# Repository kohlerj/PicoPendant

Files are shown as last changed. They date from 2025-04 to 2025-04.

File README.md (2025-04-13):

# PicoPendant

## Description

Inspired by the [CNC-Pendant-Firmware](https://github.com/Duet3D/CNC-Pendant-Firmware), I created a simple CNC pendant based on the cheap Raspberry Pico microcontroller to be used with Duet3D Ltd RepRapFirmware. 

It is compatible with all versions of the Pico microcontroller RP2040 and RP2350. Obviously also compatible with the boards, that is Pico 1, Pico 2, Pico W and Pico 2W.

This is the *only* the software side and some wiring instructions. We'll see if I can make a PCB for it in the future. For now you could try to reproduce [My BOM of the weekend ;)](https://github.com/kohlerj/PicoPendant?tab=readme-ov-file#one-night-project) which ended up in the pendant you see below.

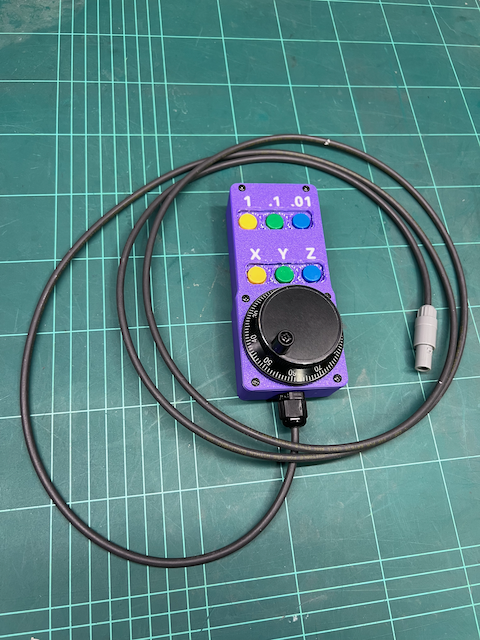
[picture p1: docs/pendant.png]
PicoPendant


## Features

- Axis selection XYZ
- Multiplier selection: 1X - 1mm, 10X - 0.1mm and 100X - 0.01mm
- Homing by holding Y for 2sec
- Reset by holding X and Z for 2sec

## An "open" BOM

A board (protoboard, PCB or some Frankenstein solution) with the following components:
- 1x Raspberry Pico (or compatible)
- 6x buttons with a normally open contact - e.g. https://www.aliexpress.com/item/32815260070.html
- 6x 5mm LEDs with adequate resistors - e.g. https://www.aliexpress.com/item/1005003144912658.html
- 1x Schottky diode (1N5819 or similar) - I'd say above 500mA to be safe, Vf as low as possible
- 2x logic level shifters to shift the encoder 5V A/B signals to 3.3V. I used LTV-817 optocouplers because it's what I had on hand. I guess a simple voltage divider would work if anything.

Aside from that you'll need:
- 1x 5V rotary encoder - e.g. https://www.aliexpress.com/item/1005008202737088.html
- A case, 3D printed most probably
- wires, cables, connectors and some screws

The Pico has a built-in Schmitt trigger action, enough for our purpose. No need to filter the inputs.

## Installation

1. Connect your pendant to a **3.3V compatible UART port** on your mainboard
    - You might need to define a new serial port in your `board.txt` file, e.g. by adding  `serial.aux2.rxTxPins={E.7, E.8}` to `board.txt`.
2. Add the following to your `config.g` file: 

```
M575 P1 S4 B57600 
```

  - P1 is the serial port number. Look at your board.txt for "aux" if you need another UART interface than the TFT or PanelDue dedicated one
  - S4 is required as we are using CRC to check for data integrity
  - B57600 is as configured in the precompiled version. You might need to adapt if you modify the code

3. That's it!

## One night project

I did not want to wait for a PCB so I went ahead a built a prototype on a protoboard together with a 3D printed case.

### BOM

 I used the following components:

- 1x protoboard 50x70mm, https://www.aliexpress.com/item/1005001854661430.html
- 1x Pico 2 board, https://www.digikey.ch/short/4wzqqnww
- 6x buttons, https://www.aliexpress.com/item/32815260070.html
- 6x LEDs with 100Ohm for the blue and 220Ohm resistors for the green LEDs, https://www.aliexpress.com/item/1005003144912658.html
- 1x Schottky diode (1N5819), https://www.digikey.ch/short/5j751j2j
- 2x LTV-817 DIP-4 optocouplers with 2x 1k resistors for the photodiode side, https://www.digikey.ch/short/rwcv58q7
- 1x 5V rotary encoder, https://www.aliexpress.com/item/1005008202737088.html
- 1x PG-7 gland, https://www.aliexpress.com/item/1005003296249352.html
- 1x 3-pin fake *ODU*-like connector, https://www.aliexpress.com/item/1005002002825883.html
- 4x 2x8mm self-tapping screws
- 6x 3x8mm self-tapping screws
- wires, cables, connectors

### Pins

The pre-compiled version uses the pinout found in the table below.

| Pin | Function | Comment |
|-----|---|---|
| GP0  | UART_TX | **3.3V** |
| GP4  | X axis LED | |
| GP5  | X axis button | internally pulled-up |
| GP10 | encoder A | **3.3V** |
| GP11 | encoder B | **3.3V** |
| GP12 | Y axis LED | |
| GP13 | Y axis button | internally pulled-up |
| GP14 | 1X LED | |
| GP15 | 1X button | internally pulled-up |
| GP16 | 10X LED | |
| GP17 | 10X button | internally pulled-up |
| GP18 | 100X LED | |
| GP19 | 100X button | internally pulled-up |
| GP20 | Z axis LED | |
| GP21 | Z axis button | internally pulled-up |
| VSYS | - | Connected to diode's **cathode** |

Refer to the [configuration section](https://github.com/kohlerj/PicoPendant/blob/main/PicoPendant.cpp#L44-L74) in `PicoPendant.cpp`.

### Wiring and schematics

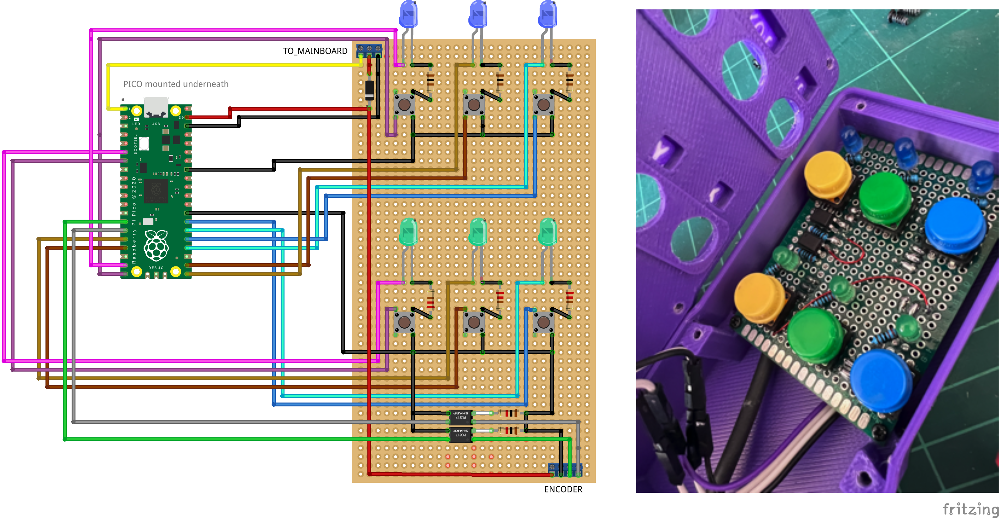
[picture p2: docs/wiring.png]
Wiring


Link to [schematics](./docs/schematics.png)

### Case

In the CAD folder, you'll find a STEP model of the case. The model includes built-in support and it is meant to be printed with a **layer height of .3mm**. It is a **multicolor** print. The letters need be printed in a translucent material while the case in an opaque one. 

If you do not have a multicolor printer, do the following:
1. Load the model with ALL subparts
2. Remove casing parts and built-in support. Keep only the letters
3. Export this job
4. Add the casing parts and built-in support back and remove the letters
5. Export this job
6. Combine the two jobs
    1. Open the first job and scroll until the end of print code is called. Remove the call and everything below
    2. Add a pause that will allow you to change the filament and come back at exactly the same spot
    3. Copy in the content of the second job
    4. Remove everything up to and including the print start code. 
    5. Tweak the code so that after the pause, the printer will move to the start position of the second job
    6. **Make sure nothing is overlapping**, the skirt in particular if you are using one!!!

The dimensions are **NOT** compensated for ABS, my material of choice. This means that it should print just fine on filament that shrinks less. For ABS, use your material shrinkage parameter or scale up the XY axes by 1%.

Support should come off easily with a flat screwdriver.

You might need to clear up the button holes a little bit. I made them already larger than my prototype but it is untested.

## License

This project is licensed under the MIT License - see the [LICENSE](LICENSE.txt) file for details.

In contains code from the Pico examples repository under BSD-3 license. See the [LICENSE](LICENSE.txt) file for details.

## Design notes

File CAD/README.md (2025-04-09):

# OnShape

The case was designed on OnShape: [Pendant](https://cad.onshape.com/documents/d751ca49352ebbe916205d74/w/4706b7efb3b0ea69cdef4548/e/34748dad4fb093fe07ba34ad)

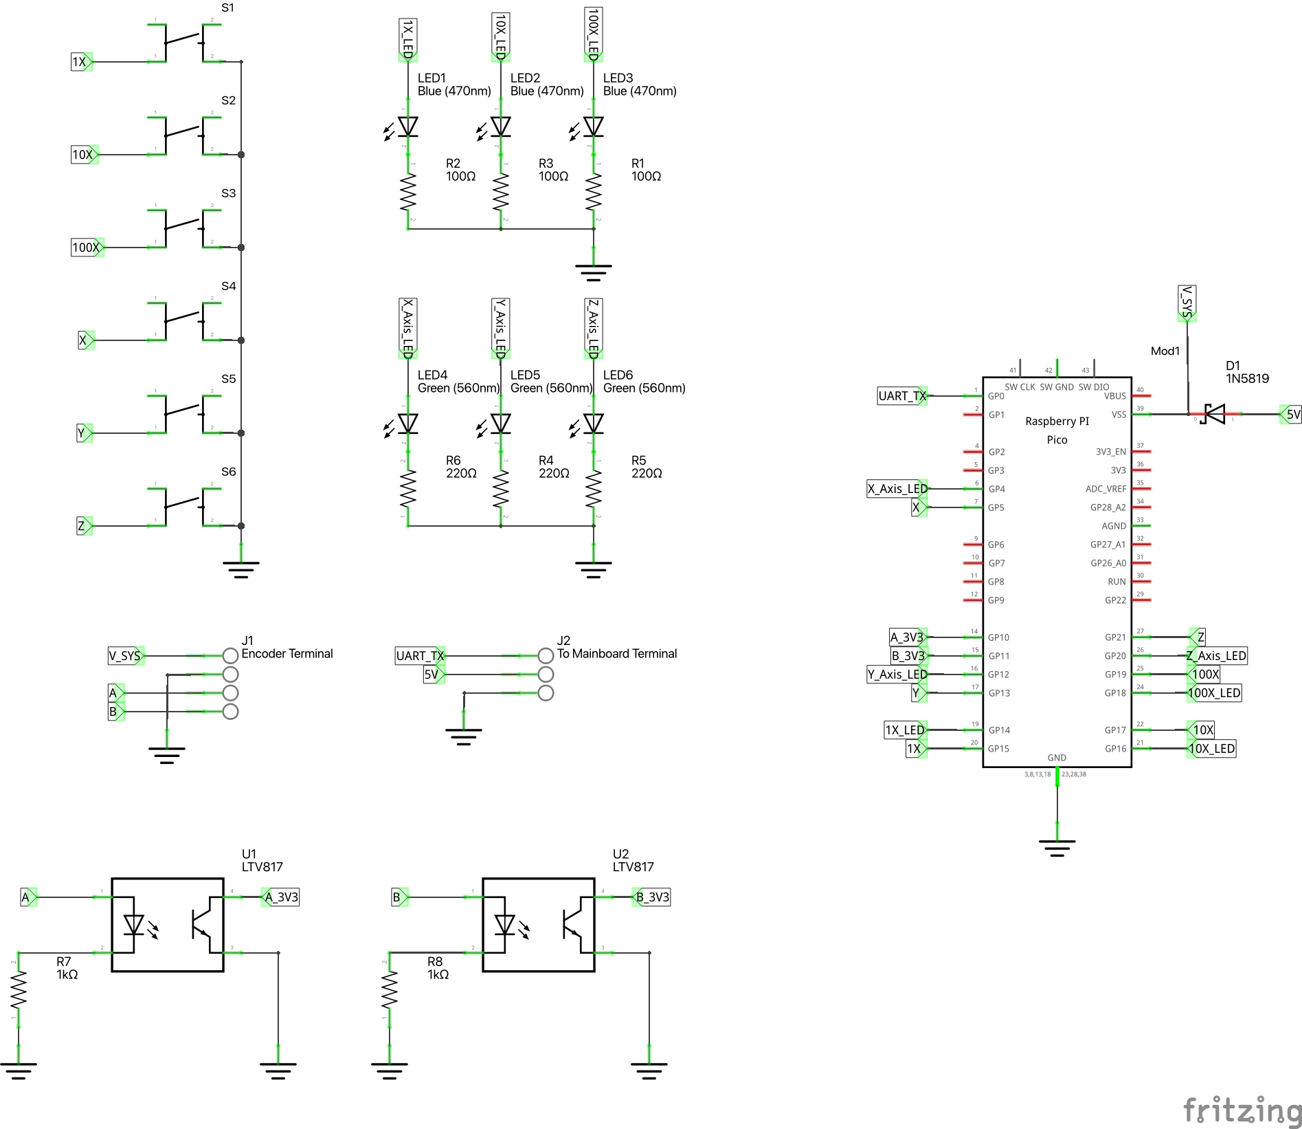
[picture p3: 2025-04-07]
docs/schematics.png

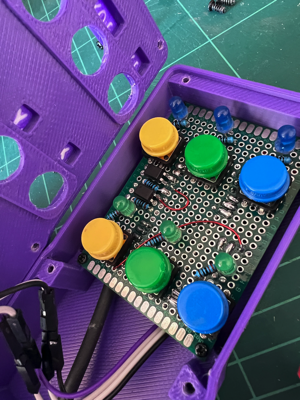
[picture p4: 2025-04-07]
docs/internals.png

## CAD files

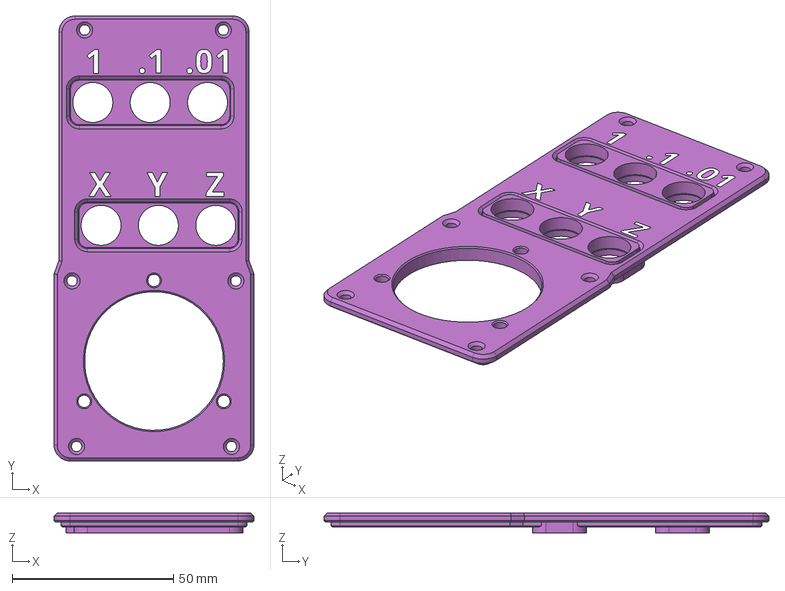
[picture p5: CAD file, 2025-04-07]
CAD/Cover.step
62.0 x 138.0 x 6.20 mm

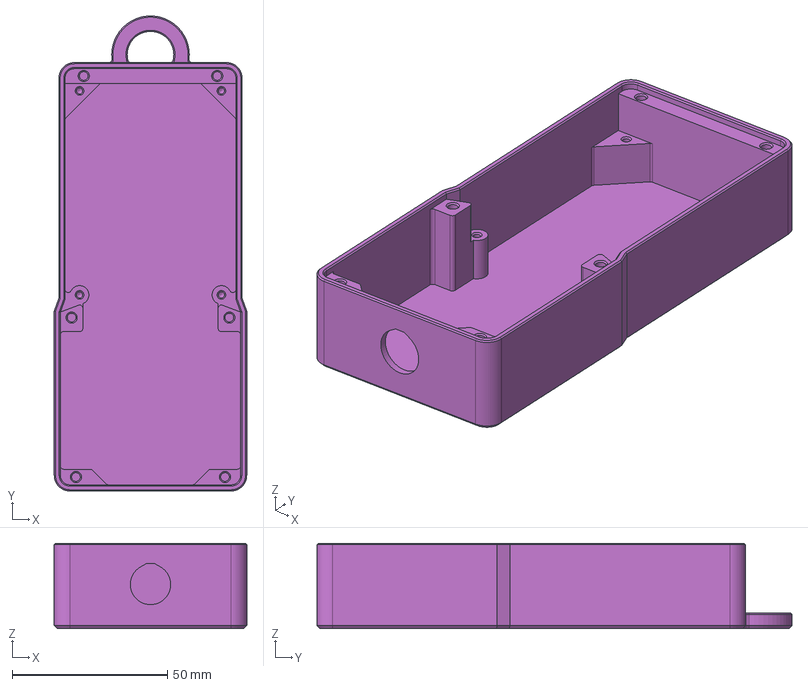
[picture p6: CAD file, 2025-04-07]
CAD/Base.step
62.0 x 153.0 x 27.5 mm

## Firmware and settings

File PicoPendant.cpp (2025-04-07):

/*******************************************************************************
 * File:        PicoPendant.cpp
 * Author:      Julien Kohler
 * Created:     2025-04-07
 *
 * Description: Based on CNC-Pendant from Duet and Raspberry Pi Pico Encoder
 *              example.
 * 
 *              Simply add M575 P1 S4 B57600 to your config.g file to enable the
 *              Duet3D pendant support.
 *              P is the serial port number
 *              S4 is the mode. This project uses CRC so mode 4 is required.
 *              B57600 is the baudrate that needs to match the value below
 *              
 *              User can select the axis and the multiplier using the buttons.
 *              The encoder is used to move the selected axis.
 *              The selected axis is indicated by the corresponding LED.
 *              The selected multiplier is indicated by the corresponding LED.
 * 
 *              The user can reset the printer by pressing the X and Z buttons for 
 *              2 seconds.
 * 
 *              The user can home the printer by pressing the Y button for 2 seconds.
 *           
 *
 * License:     This file is subject to the terms and conditions outlined in the
 *              LICENSE file located at the root of this project.
 *              (The LICENSE file may specify MIT, GPL, or another license.)
 ******************************************************************************/

#include <stdio.h>
#include "pico/stdlib.h"
#include "hardware/pio.h"
#include "hardware/timer.h"
#include "hardware/gpio.h"

#include "quadrature_encoder.pio.h"
#include <string>
#include <string_view>
#include <format>

#define UART uart0

/* Configuration */
static constexpr uint8_t kUartTxPin = 0;
static constexpr uint8_t kUartRxPin = 1;
static constexpr uint32_t kUartBaudRate = 57600; // default Duet3D baud rate for pendant

static constexpr uint8_t kPinAb = 10; // needs to be subsequent pins, e.g. 10-11

static constexpr uint8_t kPin1x = 15;
static constexpr uint8_t kPin1xLed = 14;
static constexpr uint8_t kPin10x = 17;
static constexpr uint8_t kPin10xLed = 16;
static constexpr uint8_t kPin100x = 19;
static constexpr uint8_t kPin100xLed = 18;

static constexpr uint8_t kPinXAxis = 5;
static constexpr uint8_t kPinXAxisLed = 4;
static constexpr uint8_t kPinYAxis = 13;
static constexpr uint8_t kPinYAxisLed = 12;
static constexpr uint8_t kPinZAxis = 21;
static constexpr uint8_t kPinZAxisLed = 20;

static constexpr uint16_t kLongPressLoopDurationInUs = 1000;
static constexpr uint16_t kResetLoopsToTimeout = 2000; // 2000 * 1000us = 2s
static constexpr uint16_t kResetLoopsToToggleLeds = 100; // 100 * 1000us = 100ms
static constexpr uint16_t kHomeLoopsToTimeout = 2000; // 2000 * 1000us = 2s
static constexpr uint16_t kDelayAfterLongPressCommandInMs = 500;

static constexpr int64_t kMinimumTimeBtwCommands = 20 * 1000;  // 20ms
static constexpr int64_t kAccumulatedDeltaDieOutTime =
    kMinimumTimeBtwCommands * 10;  // 10 times the minimum time
/* End of configuration */

static constexpr uint8_t kPulsesPerClick = 4;

static constexpr const char* kMoveCommands[] = {
    "G91 G0 F6000 X",  // X axis
    "G91 G0 F6000 Y",  // Y axis
    "G91 G0 F600 Z",   // Z axis
};

static const uint16_t __not_in_flash("crcdata") kCrc16Table[] = {
    0x0000, 0x1021, 0x2042, 0x3063, 0x4084, 0x50a5, 0x60c6, 0x70e7, 0x8108,
    0x9129, 0xa14a, 0xb16b, 0xc18c, 0xd1ad, 0xe1ce, 0xf1ef, 0x1231, 0x0210,
    0x3273, 0x2252, 0x52b5, 0x4294, 0x72f7, 0x62d6, 0x9339, 0x8318, 0xb37b,
    0xa35a, 0xd3bd, 0xc39c, 0xf3ff, 0xe3de, 0x2462, 0x3443, 0x0420, 0x1401,
    0x64e6, 0x74c7, 0x44a4, 0x5485, 0xa56a, 0xb54b, 0x8528, 0x9509, 0xe5ee,
    0xf5cf, 0xc5ac, 0xd58d, 0x3653, 0x2672, 0x1611, 0x0630, 0x76d7, 0x66f6,
    0x5695, 0x46b4, 0xb75b, 0xa77a, 0x9719, 0x8738, 0xf7df, 0xe7fe, 0xd79d,
    0xc7bc, 0x48c4, 0x58e5, 0x6886, 0x78a7, 0x0840, 0x1861, 0x2802, 0x3823,
    0xc9cc, 0xd9ed, 0xe98e, 0xf9af, 0x8948, 0x9969, 0xa90a, 0xb92b, 0x5af5,
    0x4ad4, 0x7ab7, 0x6a96, 0x1a71, 0x0a50, 0x3a33, 0x2a12, 0xdbfd, 0xcbdc,
    0xfbbf, 0xeb9e, 0x9b79, 0x8b58, 0xbb3b, 0xab1a, 0x6ca6, 0x7c87, 0x4ce4,
    0x5cc5, 0x2c22, 0x3c03, 0x0c60, 0x1c41, 0xedae, 0xfd8f, 0xcdec, 0xddcd,
    0xad2a, 0xbd0b, 0x8d68, 0x9d49, 0x7e97, 0x6eb6, 0x5ed5, 0x4ef4, 0x3e13,
    0x2e32, 0x1e51, 0x0e70, 0xff9f, 0xefbe, 0xdfdd, 0xcffc, 0xbf1b, 0xaf3a,
    0x9f59, 0x8f78, 0x9188, 0x81a9, 0xb1ca, 0xa1eb, 0xd10c, 0xc12d, 0xf14e,
    0xe16f, 0x1080, 0x00a1, 0x30c2, 0x20e3, 0x5004, 0x4025, 0x7046, 0x6067,
    0x83b9, 0x9398, 0xa3fb, 0xb3da, 0xc33d, 0xd31c, 0xe37f, 0xf35e, 0x02b1,
    0x1290, 0x22f3, 0x32d2, 0x4235, 0x5214, 0x6277, 0x7256, 0xb5ea, 0xa5cb,
    0x95a8, 0x8589, 0xf56e, 0xe54f, 0xd52c, 0xc50d, 0x34e2, 0x24c3, 0x14a0,
    0x0481, 0x7466, 0x6447, 0x5424, 0x4405, 0xa7db, 0xb7fa, 0x8799, 0x97b8,
    0xe75f, 0xf77e, 0xc71d, 0xd73c, 0x26d3, 0x36f2, 0x0691, 0x16b0, 0x6657,
    0x7676, 0x4615, 0x5634, 0xd94c, 0xc96d, 0xf90e, 0xe92f, 0x99c8, 0x89e9,
    0xb98a, 0xa9ab, 0x5844, 0x4865, 0x7806, 0x6827, 0x18c0, 0x08e1, 0x3882,
    0x28a3, 0xcb7d, 0xdb5c, 0xeb3f, 0xfb1e, 0x8bf9, 0x9bd8, 0xabbb, 0xbb9a,
    0x4a75, 0x5a54, 0x6a37, 0x7a16, 0x0af1, 0x1ad0, 0x2ab3, 0x3a92, 0xfd2e,
    0xed0f, 0xdd6c, 0xcd4d, 0xbdaa, 0xad8b, 0x9de8, 0x8dc9, 0x7c26, 0x6c07,
    0x5c64, 0x4c45, 0x3ca2, 0x2c83, 0x1ce0, 0x0cc1, 0xef1f, 0xff3e, 0xcf5d,
    0xdf7c, 0xaf9b, 0xbfba, 0x8fd9, 0x9ff8, 0x6e17, 0x7e36, 0x4e55, 0x5e74,
    0x2e93, 0x3eb2, 0x0ed1, 0x1ef0};

volatile bool update_leds = true;

enum class Axes : uint8_t {
  kX = 0,
  kY = 1,
  kZ = 2,
};

volatile Axes current_axis = Axes::kX;

namespace multiplier {
static constexpr float k1X = 1.0F;
static constexpr float k10X = 0.1F;
static constexpr float k100X = 0.01F;
}  // namespace multiplier

volatile float current_multiplier = multiplier::k1X;

void __isr GpioCallback(uint gpio, uint32_t events) {
  if (gpio == kPin1x) {
    current_multiplier = multiplier::k1X;
  } else if (gpio == kPin10x) {
    current_multiplier = multiplier::k10X;
  } else if (gpio == kPin100x) {
    current_multiplier = multiplier::k100X;
  } else if (gpio == kPinXAxis) {
    current_axis = Axes::kX;
  } else if (gpio == kPinYAxis) {
    current_axis = Axes::kY;
  } else if (gpio == kPinZAxis) {
    current_axis = Axes::kZ;
  }

  update_leds = true;
}

void LedIntro();
void CheckResetRequest();
void CheckHomingRequest();
uint16_t ComputeCrc16(const std::string_view& data);
void SendCommand(const std::string_view& command);
void UpdateLeds();

int main() {
  int32_t new_value = 0;
  int32_t delta = 0;
  int32_t accumulated_delta = 0;
  int32_t line_number = 0;
  uint32_t long_press_counter = 0;

  absolute_time_t now = 0;
  absolute_time_t last_command_time = 0;
  absolute_time_t last_movement_time = 0;

  uart_init(UART, kUartBaudRate);
  gpio_set_function(kUartTxPin, UART_FUNCSEL_NUM(UART, kUartTxPin));
  gpio_set_function(kUartRxPin, UART_FUNCSEL_NUM(UART, kUartRxPin));

  PIO pio;
  uint sm;
  pio_claim_free_sm_and_add_program(&quadrature_encoder_program, &pio, &sm, NULL);
  quadrature_encoder_program_init(pio, sm, kPinAb, 0);

  gpio_init(kPin1x);
  gpio_pull_up(kPin1x);
  gpio_init(kPin1xLed);
  gpio_set_dir(kPin1xLed, GPIO_OUT != 0U);

  gpio_init(kPin10x);
  gpio_pull_up(kPin10x);
  gpio_init(kPin10xLed);
  gpio_set_dir(kPin10xLed, GPIO_OUT != 0U);

  gpio_init(kPin100x);
  gpio_pull_up(kPin100x);
  gpio_init(kPin100xLed);
  gpio_set_dir(kPin100xLed, GPIO_OUT != 0U);

  gpio_init(kPinXAxis);
  gpio_pull_up(kPinXAxis);
  gpio_init(kPinXAxisLed);
  gpio_set_dir(kPinXAxisLed, GPIO_OUT != 0U);

  gpio_init(kPinYAxis);
  gpio_pull_up(kPinYAxis);
  gpio_init(kPinYAxisLed);
  gpio_set_dir(kPinYAxisLed, GPIO_OUT != 0U);

  gpio_init(kPinZAxis);
  gpio_pull_up(kPinZAxis);
  gpio_init(kPinZAxisLed);
  gpio_set_dir(kPinZAxisLed, GPIO_OUT != 0U);

  LedIntro();

  gpio_set_irq_enabled_with_callback(kPin1x, GPIO_IRQ_EDGE_FALL, true,
                                     &GpioCallback);
  gpio_set_irq_enabled_with_callback(kPin10x, GPIO_IRQ_EDGE_FALL, true,
                                     &GpioCallback);
  gpio_set_irq_enabled_with_callback(kPin100x, GPIO_IRQ_EDGE_FALL, true,
                                     &GpioCallback);
  gpio_set_irq_enabled_with_callback(kPinXAxis, GPIO_IRQ_EDGE_FALL, true,
                                     &GpioCallback);
  gpio_set_irq_enabled_with_callback(kPinYAxis, GPIO_IRQ_EDGE_FALL, true,
                                     &GpioCallback);
  gpio_set_irq_enabled_with_callback(kPinZAxis, GPIO_IRQ_EDGE_FALL, true,
                                     &GpioCallback);

  while (true) {
    CheckResetRequest();

    CheckHomingRequest();

    now = get_absolute_time();

    new_value = quadrature_encoder_get_count(pio, sm);
    static int32_t old_value = new_value;

    delta = new_value - old_value;
    if (delta != 0) {
      last_movement_time = now;
    }
    
    accumulated_delta += delta;
    old_value = new_value;

    if (absolute_time_diff_us(last_command_time, now) >
        kMinimumTimeBtwCommands) {
      if (abs(accumulated_delta) >= kPulsesPerClick) {
        int32_t sending_delta = accumulated_delta / kPulsesPerClick;
        accumulated_delta -= kPulsesPerClick * sending_delta;

        std::string command = kMoveCommands[static_cast<uint8_t>(current_axis)];
        command += std::format("{:.2f}", sending_delta * current_multiplier);

        SendCommand(command);

        last_command_time = now;
      }
    }

    if (absolute_time_diff_us(last_movement_time, now) >
        kAccumulatedDeltaDieOutTime) {
      accumulated_delta = 0;
    }

    UpdateLeds();
  }
}

void UpdateLeds() {
  if (update_leds) {
    update_leds = false;

    // Turn on the LED for the current multiplier
    if (current_multiplier == multiplier::k1X) {
      gpio_put(kPin1xLed, true);
      gpio_put(kPin10xLed, false);
      gpio_put(kPin100xLed, false);
    } else if (current_multiplier == multiplier::k10X) {
      gpio_put(kPin1xLed, false);
      gpio_put(kPin10xLed, true);
      gpio_put(kPin100xLed, false);
    } else if (current_multiplier == multiplier::k100X) {
      gpio_put(kPin1xLed, false);
      gpio_put(kPin10xLed, false);
      gpio_put(kPin100xLed, true);
    }
    // Turn on the LED for the current axis
    if (current_axis == Axes::kX) {
      gpio_put(kPinXAxisLed, true);
      gpio_put(kPinYAxisLed, false);
      gpio_put(kPinZAxisLed, false);
    } else if (current_axis == Axes::kY) {
      gpio_put(kPinXAxisLed, false);
      gpio_put(kPinYAxisLed, true);
      gpio_put(kPinZAxisLed, false);
    } else if (current_axis == Axes::kZ) {
      gpio_put(kPinXAxisLed, false);
      gpio_put(kPinYAxisLed, false);
      gpio_put(kPinZAxisLed, true);
    }
  }
}

void CheckResetRequest() {
  uint16_t long_press_counter = 0;
  bool leds_on = true;
  while (!gpio_get(kPinXAxis) && !gpio_get(kPinZAxis) && gpio_get(kPinYAxis)) {
    long_press_counter++;
    leds_on =
        long_press_counter % kResetLoopsToToggleLeds == 0 ? !leds_on : leds_on;
    gpio_put(kPinXAxisLed, leds_on);
    gpio_put(kPinZAxisLed, leds_on);
    gpio_put(kPinYAxisLed, leds_on);
    if (long_press_counter > kResetLoopsToTimeout) {
      std::string command = "M999";
      SendCommand(command);
      current_axis = Axes::kX;
      sleep_ms(kDelayAfterLongPressCommandInMs);
      break;
    }
    sleep_us(kLongPressLoopDurationInUs);
  }
  update_leds = true;
}

void CheckHomingRequest() {
  uint16_t long_press_counter = 0;
  while (!gpio_get(kPinYAxis) && gpio_get(kPinXAxis) && gpio_get(kPinZAxis)) {
    long_press_counter++;
    static constexpr uint16_t kInterval = kHomeLoopsToTimeout / 4;
    if (long_press_counter < kInterval) {
      gpio_put(kPinXAxisLed, false);
      gpio_put(kPinYAxisLed, false);
      gpio_put(kPinZAxisLed, false);
    } else if (long_press_counter < 2 * kInterval) {
      gpio_put(kPinXAxisLed, true);
      gpio_put(kPinYAxisLed, true);
      gpio_put(kPinZAxisLed, true);
    } else if (long_press_counter < 3 * kInterval) {
      gpio_put(kPinXAxisLed, true);
      gpio_put(kPinYAxisLed, true);
      gpio_put(kPinZAxisLed, false);
    } else if (long_press_counter < 4 * kInterval) {
      gpio_put(kPinXAxisLed, true);
      gpio_put(kPinYAxisLed, false);
      gpio_put(kPinZAxisLed, false);
    } else {
      gpio_put(kPinXAxisLed, false);
      gpio_put(kPinYAxisLed, false);
      gpio_put(kPinZAxisLed, false);
    }

    if (long_press_counter > kHomeLoopsToTimeout) {
      std::string command = "G28";
      SendCommand(command);
      current_axis = Axes::kX;
      sleep_ms(kDelayAfterLongPressCommandInMs);
      break;
    }
    sleep_us(kLongPressLoopDurationInUs);
  }
  update_leds = true;
}

void SendCommand(const std::string_view& command) {
  static uint32_t line_number = 0;
  static uint16_t crc = 0;

  std::string command_buffer;
  command_buffer.reserve(50);

  command_buffer = "N";
  command_buffer += std::to_string(line_number++);
  command_buffer += " ";
  command_buffer += command;
  crc = ComputeCrc16(command_buffer);
  command_buffer += "*";
  command_buffer += std::format("{:05}", crc);
  command_buffer += "\n";

  uart_default_tx_wait_blocking();
  uart_puts(UART, command_buffer.c_str());
}

void LedIntro() {
  static constexpr uint32_t kOnDurationUs = 50 * 1000;
  static constexpr uint32_t kOffDurationUs = 100 * 1000;

  for (int i = 0; i < 3; ++i) {
    gpio_put(kPin1xLed, true);
    sleep_us(kOnDurationUs);
    gpio_put(kPin1xLed, false);
    sleep_us(kOffDurationUs);

    gpio_put(kPin10xLed, true);
    sleep_us(kOnDurationUs);
    gpio_put(kPin10xLed, false);
    sleep_us(kOffDurationUs);

    gpio_put(kPin100xLed, true);
    sleep_us(kOnDurationUs);
    gpio_put(kPin100xLed, false);
    sleep_us(kOffDurationUs);

    gpio_put(kPinXAxisLed, true);
    sleep_us(kOnDurationUs);
    gpio_put(kPinXAxisLed, false);
    sleep_us(kOffDurationUs);

    gpio_put(kPinYAxisLed, true);
    sleep_us(kOnDurationUs);
    gpio_put(kPinYAxisLed, false);
    sleep_us(kOffDurationUs);

    gpio_put(kPinZAxisLed, true);
    sleep_us(kOnDurationUs);
    gpio_put(kPinZAxisLed, false);
    sleep_us(kOffDurationUs);
  }

  sleep_ms(200);

  gpio_put(kPin1xLed, true);
  gpio_put(kPin10xLed, true);
  gpio_put(kPin100xLed, true);
  gpio_put(kPinXAxisLed, true);
  gpio_put(kPinYAxisLed, true);
  gpio_put(kPinZAxisLed, true);

  sleep_ms(1000);

  gpio_put(kPin1xLed, false);
  gpio_put(kPin10xLed, false);
  gpio_put(kPin100xLed, false);
  gpio_put(kPinXAxisLed, false);
  gpio_put(kPinYAxisLed, false);
  gpio_put(kPinZAxisLed, false);
}

uint16_t ComputeCrc16(const std::string_view& data) {
  uint16_t crc = 0x0;  // Initial value
  for (char ch : data) {
    uint8_t byte = static_cast<uint8_t>(ch);
    crc = (crc << 8) ^ kCrc16Table[((crc >> 8) ^ byte) & 0x00ff];
  }
  return crc;
}

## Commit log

2025-04-07 Add README
    [Base.step, Cover.step, fritzing_schematic.fzz]
2025-04-09 Update project configuration and licensing details
    [fritzing_schematic.fzz]
